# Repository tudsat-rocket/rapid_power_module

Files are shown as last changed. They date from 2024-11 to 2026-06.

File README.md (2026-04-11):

# Frodo Power Module

The battery boards for the FRoDO-rockets

## Version 1

@todo

## Version 2

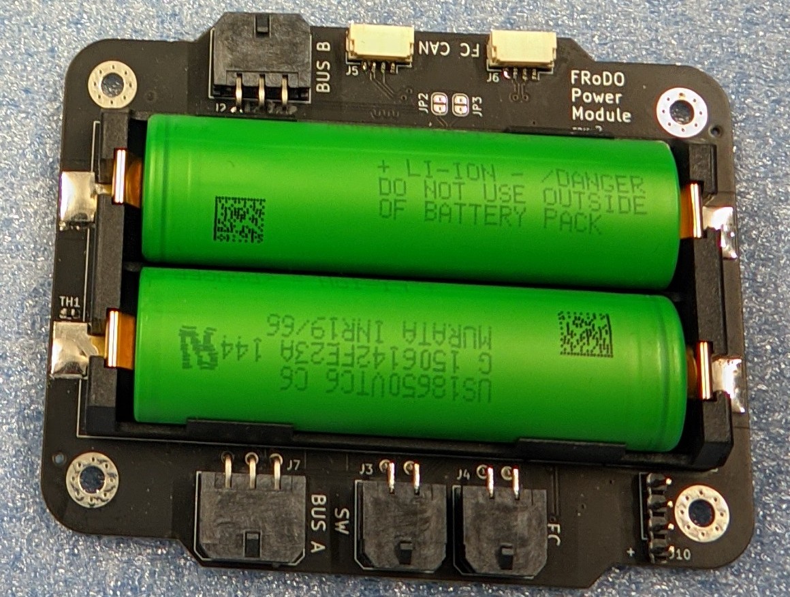
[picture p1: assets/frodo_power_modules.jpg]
battery-board


The newest version of the battery developed for the FRoDO-M-rocket 

The battery module contains two lithium-ion cells in series, mounted on an *SRAD* *PCB* using a Keystone connector, allowing the replacement of battery cells. 

The battery features a linear charging IC supporting up to 700 mA of charge current and performs balancing of the cells, powered by the charge bus through a reverse current protection diode and a PTC fuse.

### Components

- 2x 3000 mA h Sony VTC6 18650 lithium-ion cells in series
- for other components see https://github.com/tudsat-rocket/frodo_power_module/blob/main/frodo_power_module.csv

### Usage

| Connector | Purpose |
| --- | --- |
| FC | connect the flight computer. Outputs 8v with max ?a |
| SW | Switch to turn the battery board on and off |
| FC-CAN (2x) | CAN-bus for communication |
| BUS-A | |
| BUS-B | |

Spanning liegt von außen an, geht durch Arming Circuit,

## Version 3

tdb...

### ToDos for Hyacinth

- 3x 18650 lithium-ion cells in series

- New Charging IC due to more Cells

- Larger Board due to more Cells.

- Are 18650 a requirement or might they be exchanged against softbody batteries known from drones? (smaller PCB possible)

- Arming Schalter schaltet alles an.

- 

- 6 Pin durch 8 Pin ersetzen
  
  #### Possible new ICs

- https://www.ti.com/lit/ds/symlink/bq25820.pdf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

#### Ideas for Cell Voltage balancing

Good:
bq76PL536A: https://www.ti.com/lit/ds/symlink/bq76pl536a.pdf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 - Does not require host, is availabel on lcsc: https://www.lcsc.com/search?q=BQ76PL536A&s_z=n_BQ76PL536A
BQ76922: https://www.ti.com/lit/ds/symlink/bq76922.pdf?ts=1740361016781

Okay:
BQ79606A-Q1: https://www.ti.com/lit/ds/symlink/bq79606a-q1.pdf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 - Availability is bad

Meh:
BQ76925: https://www.ti.com/lit/ds/symlink/bq76925.pdf?ts=1740385881236 - due to required host. This is just an analogue expander.

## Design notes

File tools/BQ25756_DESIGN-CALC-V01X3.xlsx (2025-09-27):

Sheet: BQ2575X Design Calculator
 |  |  |  | BQ25756 Buck-Boost Battery Charger Design Calculator
 |  |  |  |  | View Password
 |  |  | = Input Box |  | BQ2575X
Step 1: Operating Specifications |  |  |  |  | Red Text = Conditional Formatting Conditions
 | Input Voltage - Min, VAC(min) | 4.2 | V | 4,2 V | 4.2 | 70
 | Input Voltage - Nom, VAC(nom) | 12 | V | 12 V | 4.2 | 70 | 4.2 | 24
 | Input Voltage - Max, VAC(max) | 24 | V | 24 V | 4.2 | 70
 | Battery Voltage, VBAT | 12.6 | V | 12,6 V | 3.3 | 70
 | Full Load Output Current, IOUT(max) | 6 | A | 6 A
 |  |  |  |  | Black Text = Lists or Formulas
Step 2: Switching Frequency
 | Desired Switching Frequency, FDFW | 500 | kHz | 500 kHz | 200 | 600
 | Recommended Switching Frequency Resistor, RFSW | 50.00 | kΩ | 50 kΩ
 | Selected Switching Frequency Resistor, RFSW | 50 | kΩ | 50 kΩ | 40 | 200
 | Recognized Switching Frequency, FSW | 500.00 | kHz |  | 475 | 525
 | Boost Duty Cycle Limitation | 88.75 | %
 | Boost Output Voltage Limitation at VAC(min) | 37.33333333 | V |  | 70 | 12.6
 | Boost Output Voltage Limitation at VAC(nom) | 70 | V |  | 70 | 12.6
 | Boost Output Voltage Limitation at VAC(max) | N/A | V |  | 70 | 12.6
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

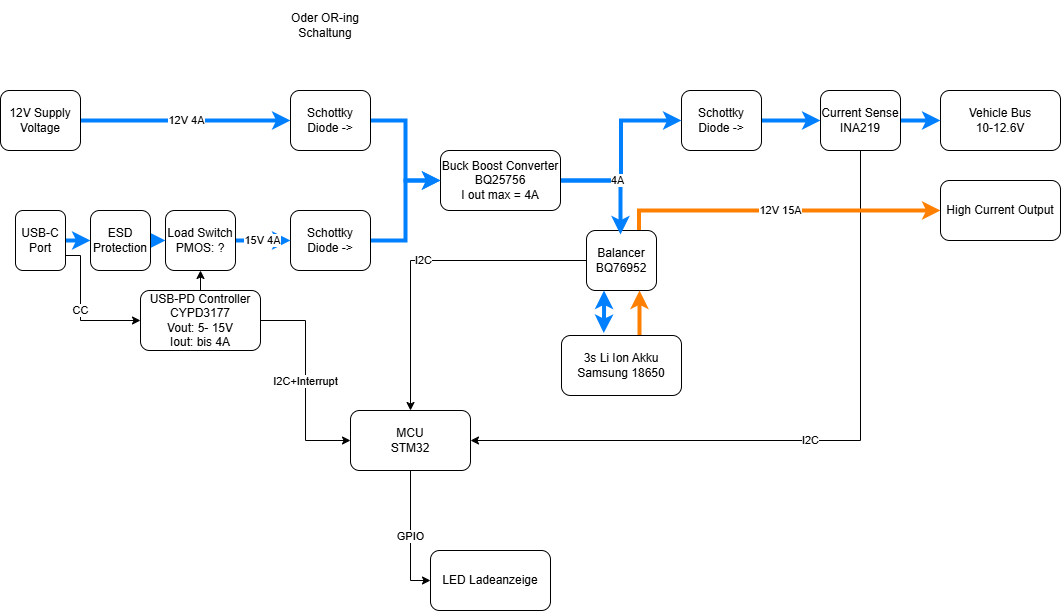
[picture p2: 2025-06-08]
docs/Power Board Overview.drawio.png

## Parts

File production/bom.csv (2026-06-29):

Designator | Footprint | Quantity | Value | LCSC Part #
C1, C2, C29, C31, C32, C33, C35, C42, C43, C44, C45, C46, C47, C48, C6, C8 | 0603 | 16 | 10u | C96446
C10, C14, C15, C16, C18, C19, C20, C21, C22, C34, C36, C41, C49, C5, C50, C51, C52 | 0402 | 17 | 100n | C307331
C11 | 1206 | 1 | 10u | C13585
C12 | 1206 | 1 | 22u | C12891
C13 | 0603 | 1 | 330n | C1615
C17, C37 | 0402 | 2 | 4u7 | C23733
C23, C27, C3, C4, C7, C9 | 0402 | 6 | 10n | C15195
C24, C26, C53, C54 | 0402 | 4 | 1u | C52923
C25, C28 | 0402 | 2 | 10p | C32949
C30 | 0805 | 1 | 2.2u | C377773
C38, C39 | 0402 | 2 | 47n | C82219
C40 | 0402 | 1 | 1n | C1523
C55 | 0402 | 1 | 100n | C1525
D1, D2, D3, D4, D5 | D_SMA | 5 | ~ | C22452
D10, D11, D12, D8, D9 | 0805 | 5 | green | C2297
D13, D6 | 0603 | 2 | red | C2286
D7 | 0805 | 1 | yellow | C2296
F1 | 2010 | 1 | 20A | C2762483
F2, F3 | 1206 | 2 | 5A | C48332
FB1 | 0603 | 1 | 120R | C14709
L1 | L_Wurth_WE-LQSH-3012 | 1 | 1u | C7423316
R1, R2, R3, R6, R7, R9 | 0402 | 6 | 22R | C25092
R10 | 0603 | 1 | 68k | C23231
R11, R13, R32, R38, R4, R5, R_TS_PU1 | 0402 | 7 | 10k | C25744
R12 | 0603 | 1 | 30k | C22984
R14, R16, R17, R18, R19, R20, R21, R22, R23, R35, R36 | 0402 | 11 | 1k | C11702
R15 | 0402 | 1 | 100k | C25741
R24 | 0603 | 1 | 2 | C22977
R25, R28 | 0402 | 2 | 10k | C25744
R26 | 0402 | 1 | 500R | C25123
R27 | 0603 | 1 | 20k | C4184
R29 | 0402 | 1 | 2k2 | C25879
R30 | 0603 | 1 | 5k24 | C23068
R31 | 0805 | 1 | 30k31 | C21841
R33 | 0402 | 1 | 100 | C25076
R34 | 2512 | 1 | 5m | C41382686
R37 | 0402 | 1 | 20k | C25765
R_IN1, R_IN2, R_IN3, R_IN4 | 0603 | 4 | 75 | C4275
R_LD1 | 0402 | 1 | 453k | C27009
SW1, SW2 | SW_SPST_TS-1088-xR020 | 2 | ~ | C720477
TP1, TP10, TP11, TP12, TP13, TP2, TP3, TP4, TP5, TP6, TP7, TP8, TP9 | TestPoint_Pad_D2.0mm | 13 | TestPoint
U1 | SOT-223-3_TabPin2 | 1 | AZ1117I-3.3 | C92102
U2 | SOT-563 | 1 | TPD4E1U06 | C527516
U3 | SOIC-8_3.9x4.9mm_P1.27mm | 1 | MCP2562-E-SN | C191417
U4 | TO-252-2 | 1 | L7805 | C58069
U5 | LQFP-64_10x10mm_P0.5mm | 1 | STM32F105RCTx | C8345
U6 | IC_BQ25798RQMR | 1 | BQ25798RQMR | C2876593
U7 | TSSOP-24_4.4x7.8mm_P0.65mm | 1 | BQ7791500PWR | C2876946
U8 | SOT-23-6 | 1 | INA181A1 | C2058943
U9 | SOT-23-5 | 1 | MCP6001-OT | C116490
Y1 | Crystal_SMD_5032-4Pin_5.0x3.2mm | 1 | 8MHz 12pF | C2149245

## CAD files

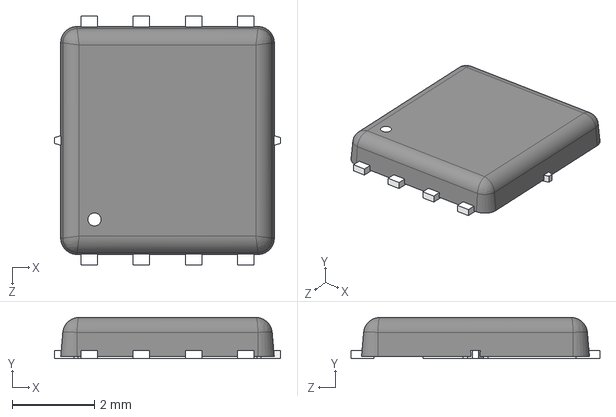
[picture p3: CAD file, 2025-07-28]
AONS66614.STEP
5.50 x 1.00 x 6.05 mm

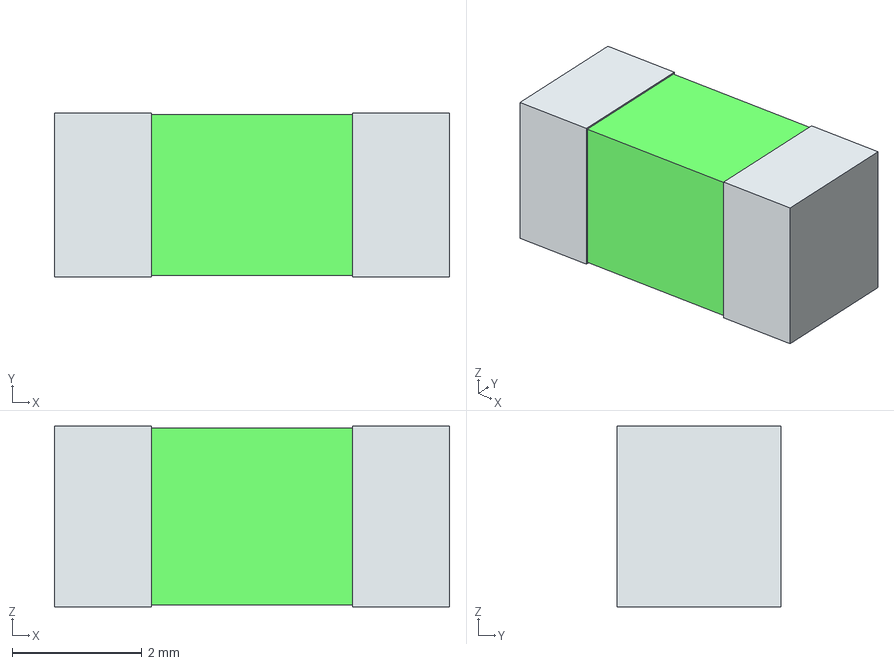
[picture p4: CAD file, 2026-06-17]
common/3dModels/Fuse_2410_0679L9200-05.stp
6.10 x 2.54 x 2.79 mm
term1
term2

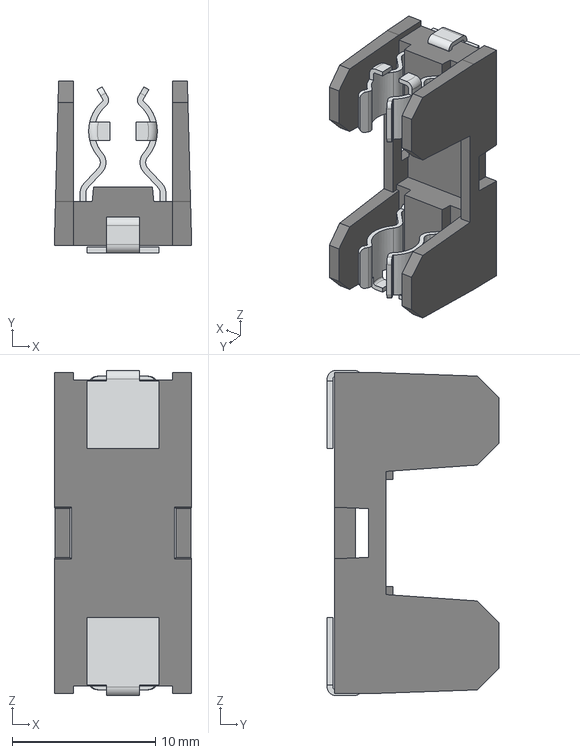
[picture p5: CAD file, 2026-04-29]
common/3dModels/Würth_fuse_holder_696103101002 (rev1).step
9.60 x 12.0 x 22.7 mm

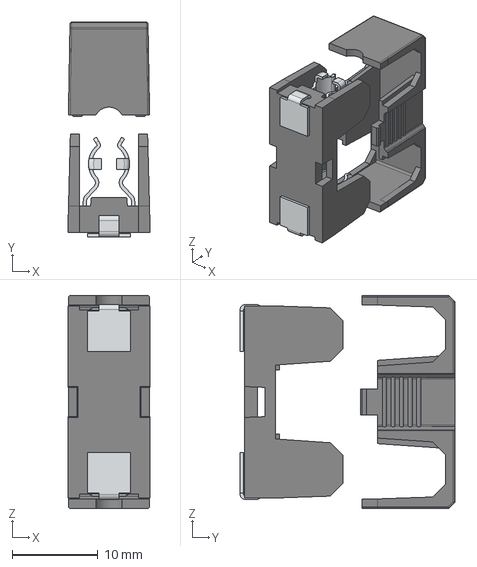
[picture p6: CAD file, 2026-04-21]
common/3dModels/20A_fuse.stp
9.60 x 25.0 x 24.8 mm
PTF18SMD
BS613

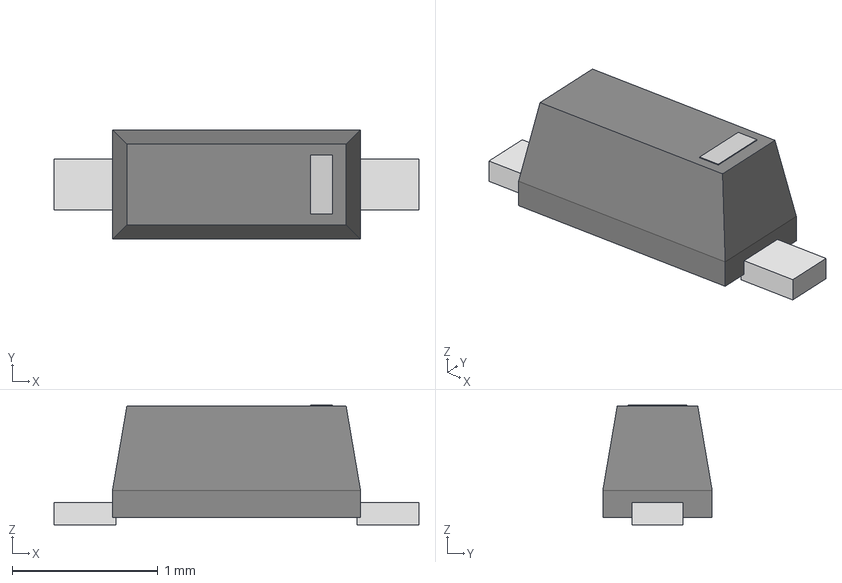
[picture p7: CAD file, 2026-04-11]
common/3dModels/SOD323F_DIO.step
2.50 x 0.75 x 0.819 mm

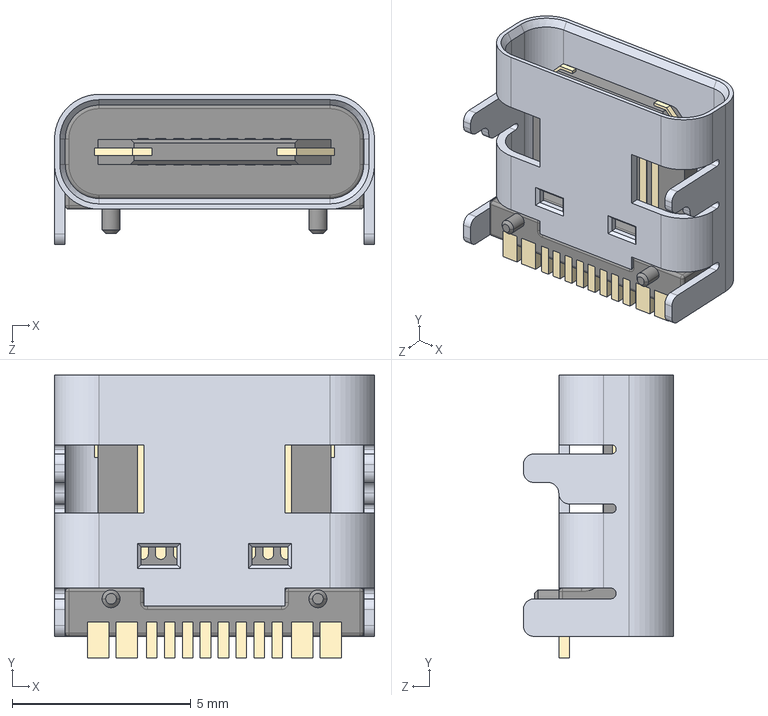
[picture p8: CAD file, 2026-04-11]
common/3dModels/usb_c.step
8.94 x 7.90 x 4.20 mm

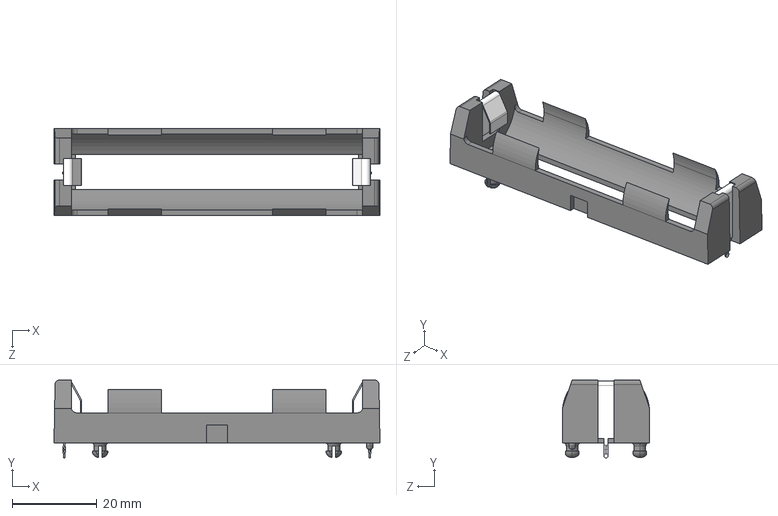
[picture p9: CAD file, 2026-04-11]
common/3dModels/Battery Holder 18650 1043.step
77.1 x 18.4 x 20.7 mm

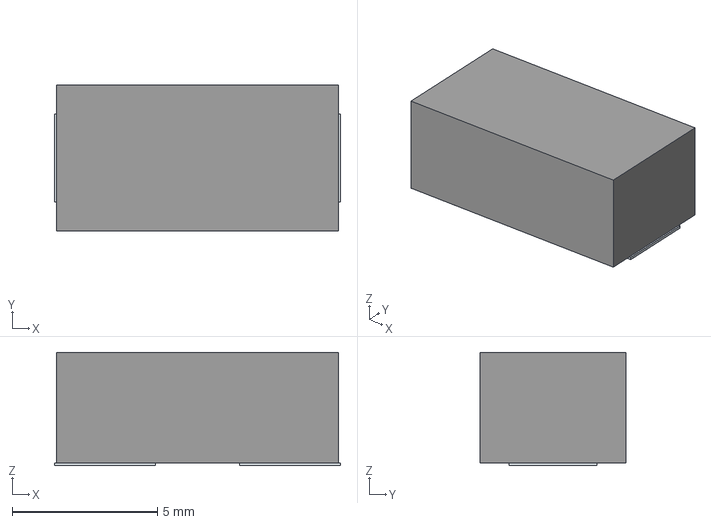
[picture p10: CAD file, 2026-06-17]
common/3dModels/0154005.stp
9.86 x 5.03 x 3.91 mm
Pins

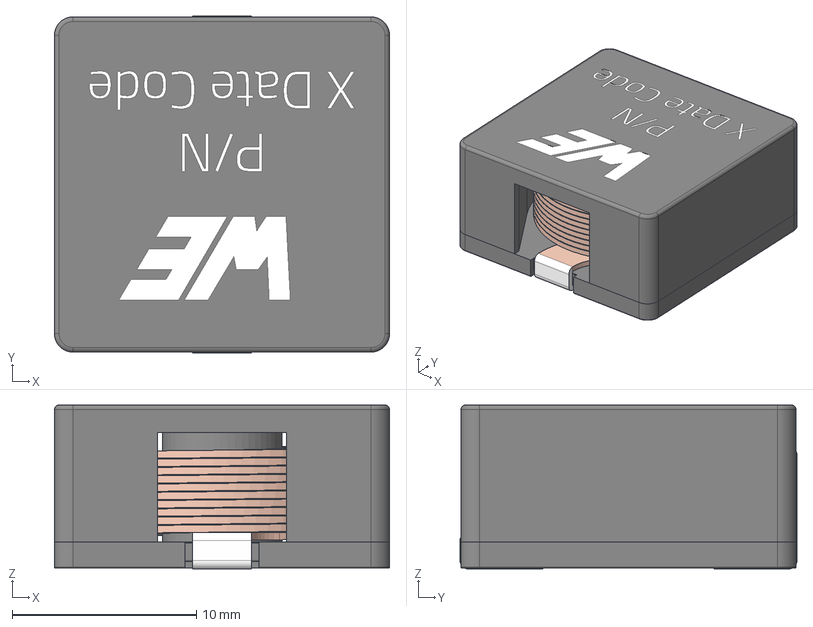
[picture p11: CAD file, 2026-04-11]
common/3dModels/o54893v246 WE-HCI_1890_7443557 (rev1).stp
18.2 x 18.3 x 8.90 mm
Gehäuse
Boden
Spule

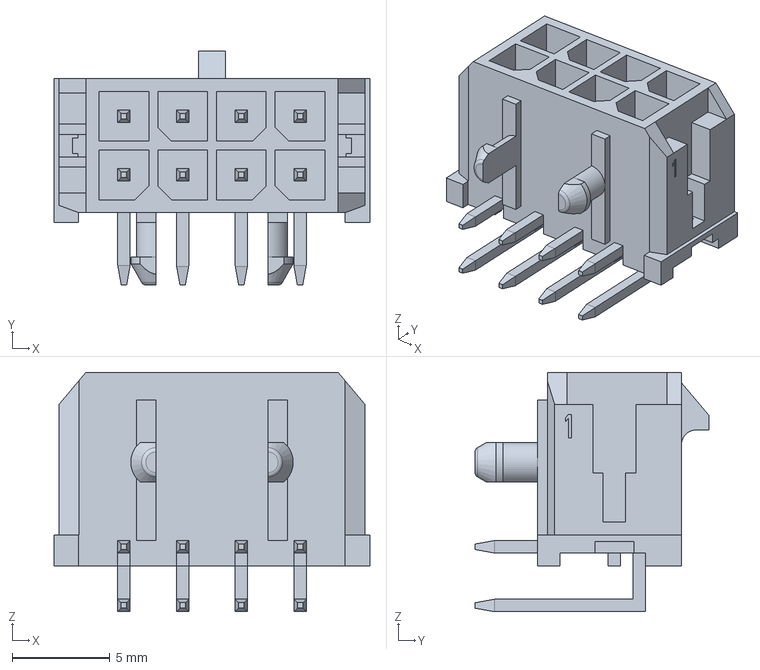
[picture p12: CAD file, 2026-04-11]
common/3dModels/430450800.stp
16.1 x 11.9 x 12.2 mm

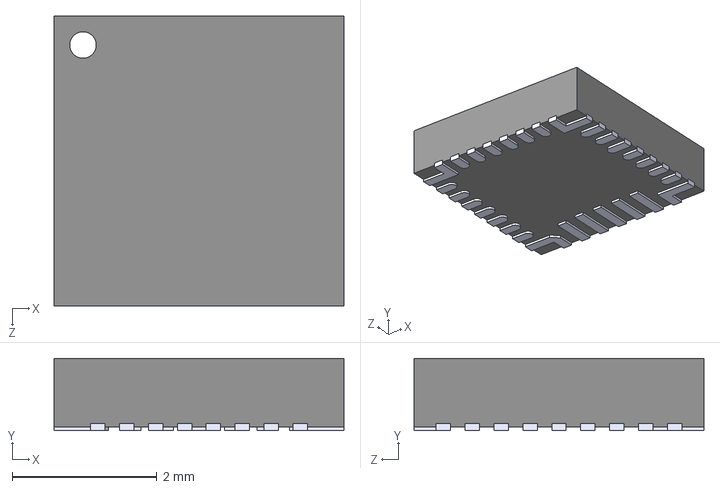
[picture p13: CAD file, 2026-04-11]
common/3dModels/BQ25798RQMR.step
4.00 x 1.00 x 4.00 mm

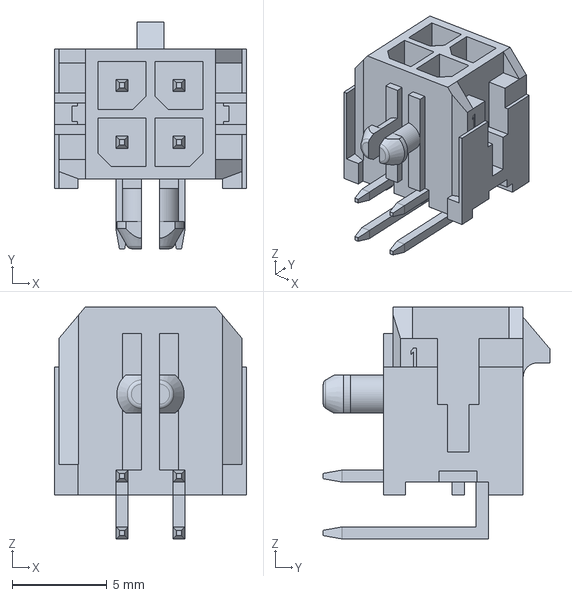
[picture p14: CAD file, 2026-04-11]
common/3dModels/430450400.step
10.2 x 11.9 x 12.2 mm

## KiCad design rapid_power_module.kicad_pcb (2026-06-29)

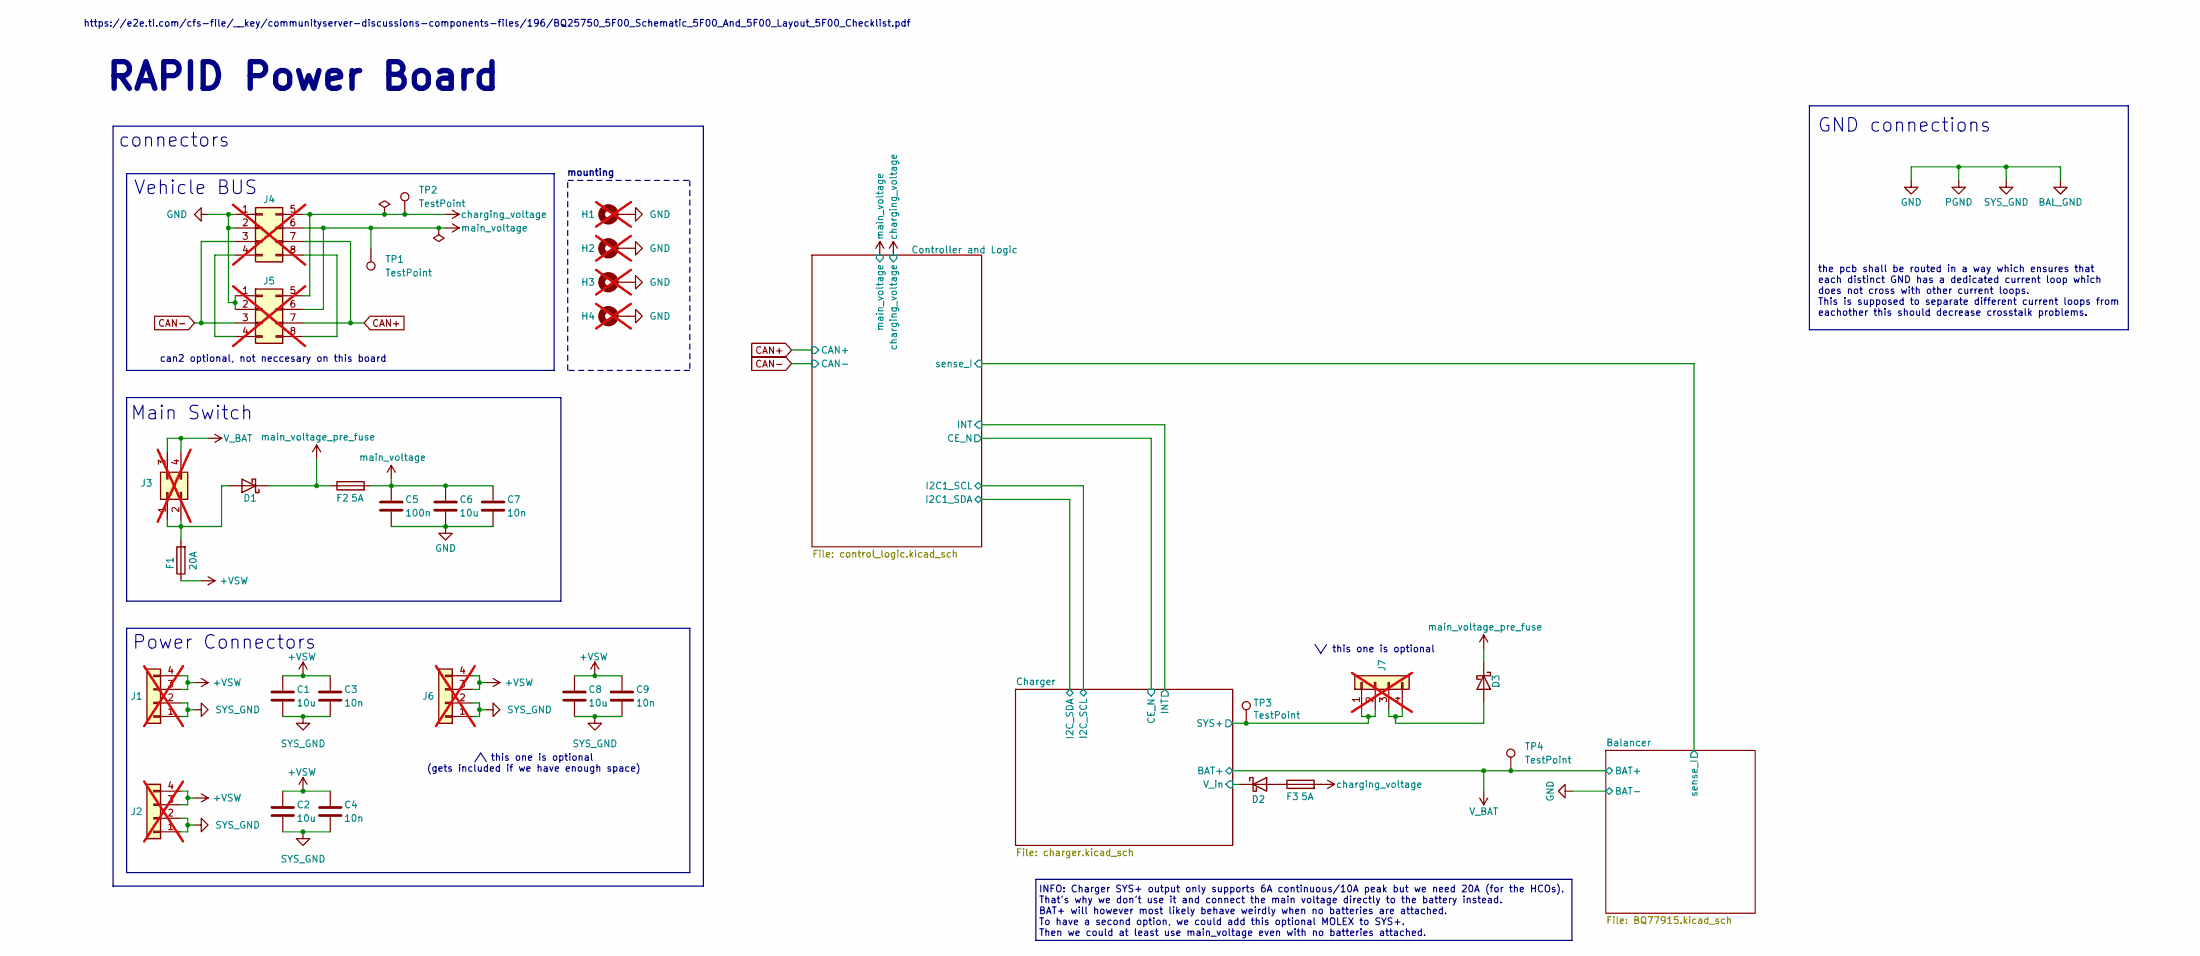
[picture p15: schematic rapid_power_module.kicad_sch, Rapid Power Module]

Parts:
C1, C2, C6, C8: 10u; C_0603_1608Metric; LCSC C96446
C3, C4, C7, C9: 10n; C_0402_1005Metric; LCSC C15195
C5: 100n; C_0402_1005Metric; LCSC C307331
D1, D2, D3: D_SMA; LCSC C22452
F1: 20A; Fuse_2010_5025Metric_Pad1.52x2.65mm_HandSolder; LCSC C2762483
F2, F3: 5A; Fuse_1206_3216Metric_Pad1.42x1.75mm_HandSolder; LCSC C48332
H1, H2, H3, H4: MountingHole_Pad; MountingHole_3.2mm_M3_Pad_Via; LCSC x; not fitted
J1, J2: Molex MicroFit 2x2; Molex_Micro-Fit_3.0_43045-0400_2x02_P3.00mm_Horizontal; Part# 0430450400; LCSC C122413; not fitted
J3: Molex MicroFit 2x2; Molex_Micro-Fit_3.0_43045-0400_2x02_P3.00mm_Horizontal; LCSC C122413; not fitted
J4, J5: Conn_02x04_Top_Bottom; Molex_Micro-Fit_3.0_43045-0800_2x04_P3.00mm_Horizontal; LCSC x; not fitted
J6, J7: Molex MicroFit 2x2; Molex_Micro-Fit_3.0_43045-0400_2x02_P3.00mm_Horizontal; Part# 0430450400; LCSC# C122413; not fitted
TP1, TP2, TP3, TP4: TestPoint; TestPoint_Pad_D2.0mm

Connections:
+VSW: C1.1, C2.1, C3.1, C4.1, C8.1, C9.1, F1.1, J1.3, J1.4, J2.3, J2.4, J6.3, J6.4
/Charger/SYS+: J7.1, J7.2, TP3.1 (1_1); also elsewhere on the board
/Charger/V_in: D2.1 (K); also elsewhere on the board
BAL_GND: C1.2, C2.2, C3.2, C4.2, C5.2, C6.2, C7.2, C8.2, C9.2, H1.1 (1_1), H2.1 (1_1), H3.1 (1_1), H4.1 (1_1), J1.1, J1.2, J2.1, J2.2, J4.1, J4.2, J5.1, J5.2, J6.1, J6.2; also elsewhere on the board
CAN+: J4.7, J5.7; also elsewhere on the board
CAN-: J4.3, J5.3; also elsewhere on the board
unnamed: D1.2 (A), F1.2, J3.1, J3.2
unnamed: D2.2 (A), F3.1
unnamed: D3.2 (A), J7.3, J7.4
unnamed: J4.4, J5.4
unnamed: J4.8, J5.8
V_BAT: J3.3, J3.4, TP4.1 (1_1); also elsewhere on the board
charging_voltage: F3.2, J4.5, J5.5, TP2.1 (1_1); also elsewhere on the board
main_voltage: C5.1, C6.1, C7.1, F2.2, J4.6, J5.6, TP1.1 (1_1); also elsewhere on the board
main_voltage_pre_fuse: D1.1 (K), D3.1 (K), F2.1

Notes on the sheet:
the pcb shall be routed in a way which ensures that each distinct GND has a dedicated current loop which does not cross with other current loops. This is supposed to separate different current loops from eachother this should decrease crosstalk problems.
connectors
can2 optional, not neccesary on this board
Vehicle BUS
Main Switch
RAPID Power Board
https://e2e.ti.com/cfs-file/__key/communityserver-discussions-components-files/196/BQ25750_5F00_Schematic_5F00_And_5F00_Layout_5F00_Checklist.pdf
\/ this one is optional
INFO: Charger SYS+ output only supports 6A continuous/10A peak but we need 20A (for the HCOs). That's why we don't use it and connect the main voltage directly to the battery instead. BAT+ will however most likely behave weirdly when no batteries are attached. To have a second option, we could add 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
mounting
/\ this one is optional (gets included if we have enough space)
Power Connectors
GND connections

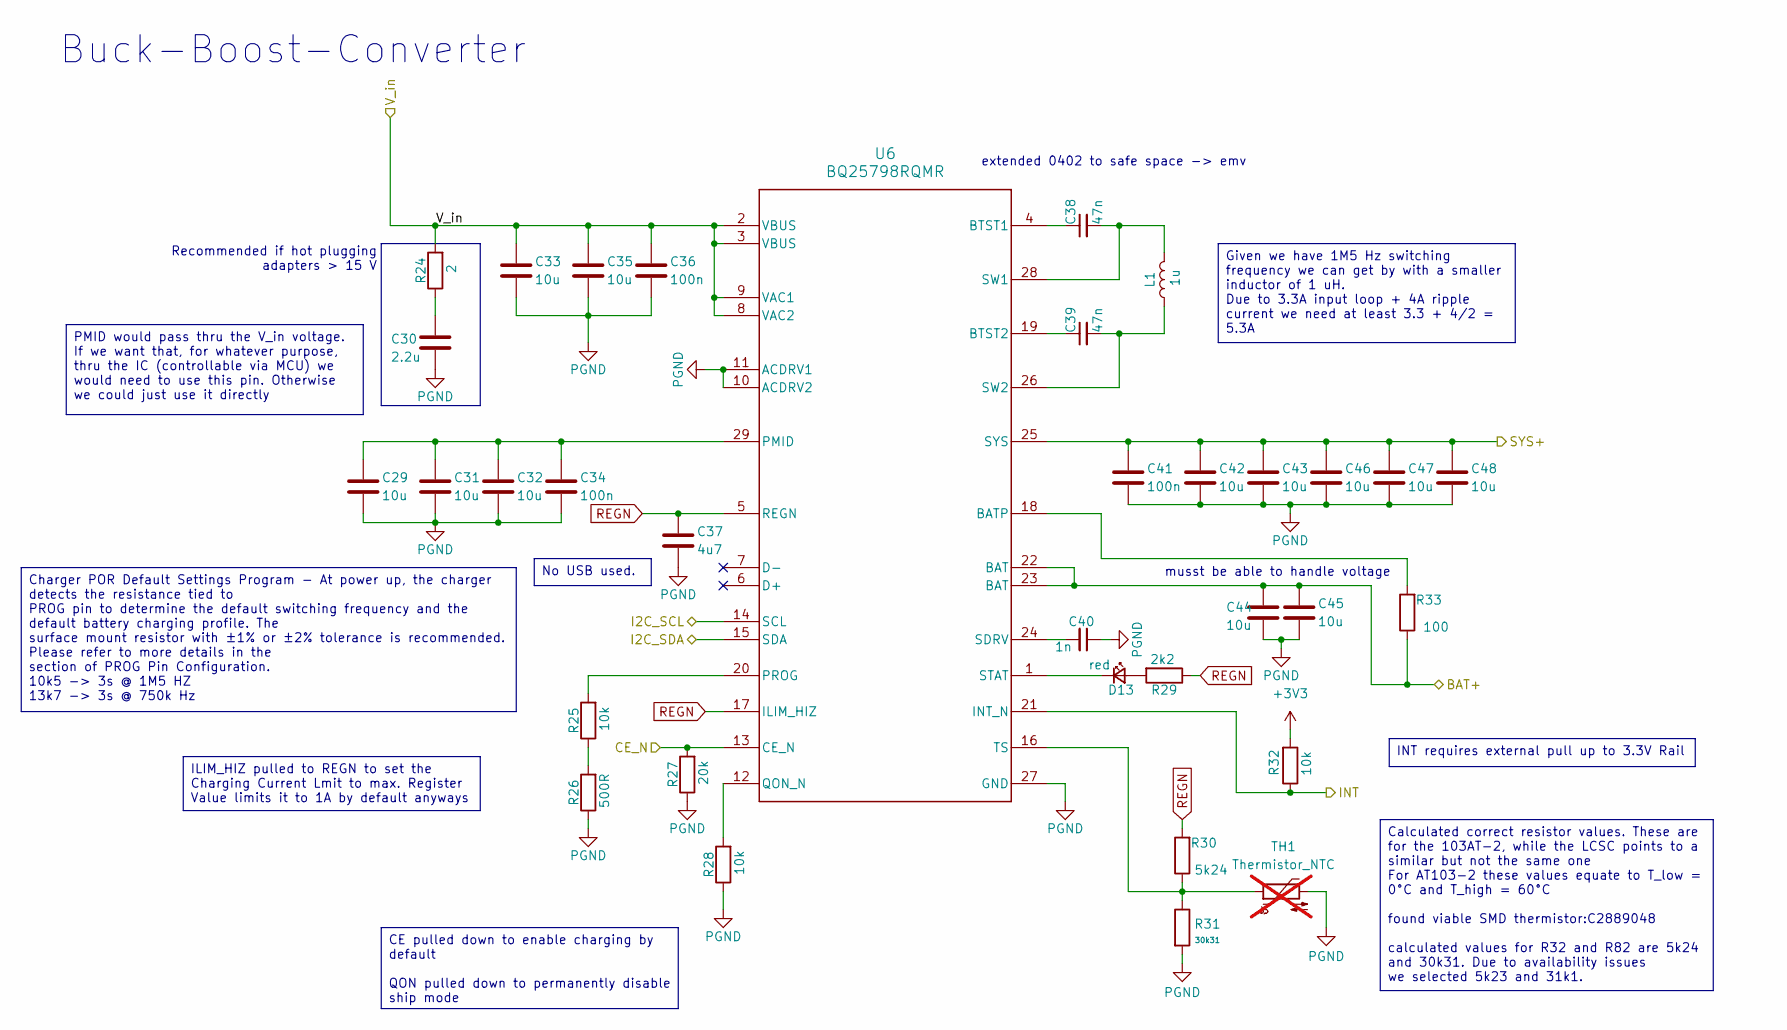
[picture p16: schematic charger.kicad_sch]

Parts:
C29, C31, C32, C33, C35, C42, C43, C44, C45, C46, C47, C48: 10u; C_0603_1608Metric; LCSC C96446
C30: 2.2u; C_0805_2012Metric; LCSC C377773
C34, C36, C41: 100n; C_0402_1005Metric; LCSC C307331
C37: 4u7; C_0402_1005Metric; LCSC C23733
C38, C39: 47n; C_0402_1005Metric; LCSC C82219
C40: 1n; C_0402_1005Metric; LCSC C1523
D13: red; LED_0603_1608Metric; LCSC C2286
L1: 1u; L_Wurth_WE-LQSH-3012; LCSC C7423316
R24: 2; R_0603_1608Metric; LCSC C22977
R25, R28, R32: 10k; R_0402_1005Metric; LCSC C25744
R26: 500R; R_0402_1005Metric; LCSC C25123
R27: 20k; R_0603_1608Metric; LCSC C4184
R29: 2k2; R_0402_1005Metric; LCSC C25879
R30: 5k24; R_0603_1608Metric; LCSC C23068
R31: 30k31; R_0805_2012Metric; LCSC C21841
R33: 100; R_0402_1005Metric; LCSC C25076
TH1: Thermistor_NTC; R_0603_1608Metric_Pad0.98x0.95mm_HandSolder; LCSC C2889048; not fitted
U6: BQ25798RQMR; IC_BQ25798RQMR; LCSC C2876593

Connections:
+3V3: R32.2; also elsewhere on the board
/Charger/CE_N: R27.2, U6.13 (CE_N); also elsewhere on the board
/Charger/INT: R32.1, U6.21 (INT_N); also elsewhere on the board
/Charger/SYS+: C41.1, C42.1, C43.1, C46.1, C47.1, C48.1, U6.25 (SYS); also elsewhere on the board
/Charger/V_in: C33.1, C35.1, C36.1, R24.2, U6.2 (VBUS), U6.3 (VBUS), U6.8 (VAC2), U6.9 (VAC1); also elsewhere on the board
BAL_GND: C29.2, C30.2, C31.2, C32.2, C33.2, C34.2, C35.2, C36.2, C37.2, C40.1, C41.2, C42.2, C43.2, C44.2, C45.2, C46.2, C47.2, C48.2, R26.1, R27.1, R28.1, R31.2, TH1.2, U6.10 (ACDRV2), U6.11 (ACDRV1), U6.27 (GND); also elsewhere on the board
I2C1_SCL: U6.14 (SCL); also elsewhere on the board
I2C1_SDA: U6.15 (SDA); also elsewhere on the board
unnamed: C30.1, R24.1
unnamed: D13.2 (A), R29.2
unnamed: D13.1 (K), U6.1 (STAT)
unnamed: R25.1, R26.2
unnamed: R33.2, U6.18 (BATP)
unnamed: C38.1, U6.4 (BTST1)
unnamed: C39.1, U6.19 (BTST2)
unnamed: C29.1, C31.1, C32.1, C34.1, U6.29 (PMID)
unnamed: R25.2, U6.20 (PROG)
unnamed: R28.2, U6.12 (QON_N)
unnamed: C40.2, U6.24 (SDRV)
unnamed: C38.2, L1.2, U6.28 (SW1)
unnamed: C39.2, L1.1, U6.26 (SW2)
unnamed: R30.1, R31.1, TH1.1, U6.16 (TS)
REGN: C37.1, R29.1, R30.2, U6.5 (REGN), U6.17 (ILIM_HIZ)
V_BAT: C44.1, C45.1, R33.1, U6.22 (BAT), U6.23 (BAT); also elsewhere on the board

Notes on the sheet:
extended 0402 to safe space -> emv
Buck-Boost-Converter
Recommended if hot plugging adapters > 15 V
musst be able to handle voltage
ILIM_HIZ pulled to REGN to set the Charging Current Lmit to max. Register Value limits it to 1A by default anyways
Given we have 1M5 Hz switching frequency we can get by with a smaller inductor of 1 uH. Due to 3.3A input loop + 4A ripple current we need at least 3.3 + 4/2 = 5.3A
INT requires external pull up to 3.3V Rail
Calculated correct resistor values. These are for the 103AT-2, while the LCSC points to a similar but not the same one For AT103-2 these values equate to T_low = 0°C and T_high = 60°C found viable SMD thermistor:C2889048 calculated values for R32 and R82 are 5k24 and 30k31. Due to availability issu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
PMID would pass thru the V_in voltage. If we want that, for whatever purpose, thru the IC (controllable via MCU) we would need to use this pin. Otherwise we could just use it directly
CE pulled down to enable charging by default QON pulled down to permanently disable ship mode
No USB used.
Charger POR Default Settings Program - At power up, the charger detects the resistance tied to PROG pin to determine the default switching frequency and the default battery charging profile. The surface mount resistor with ±1% or ±2% tolerance is recommended. Please refer to more details in the sec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

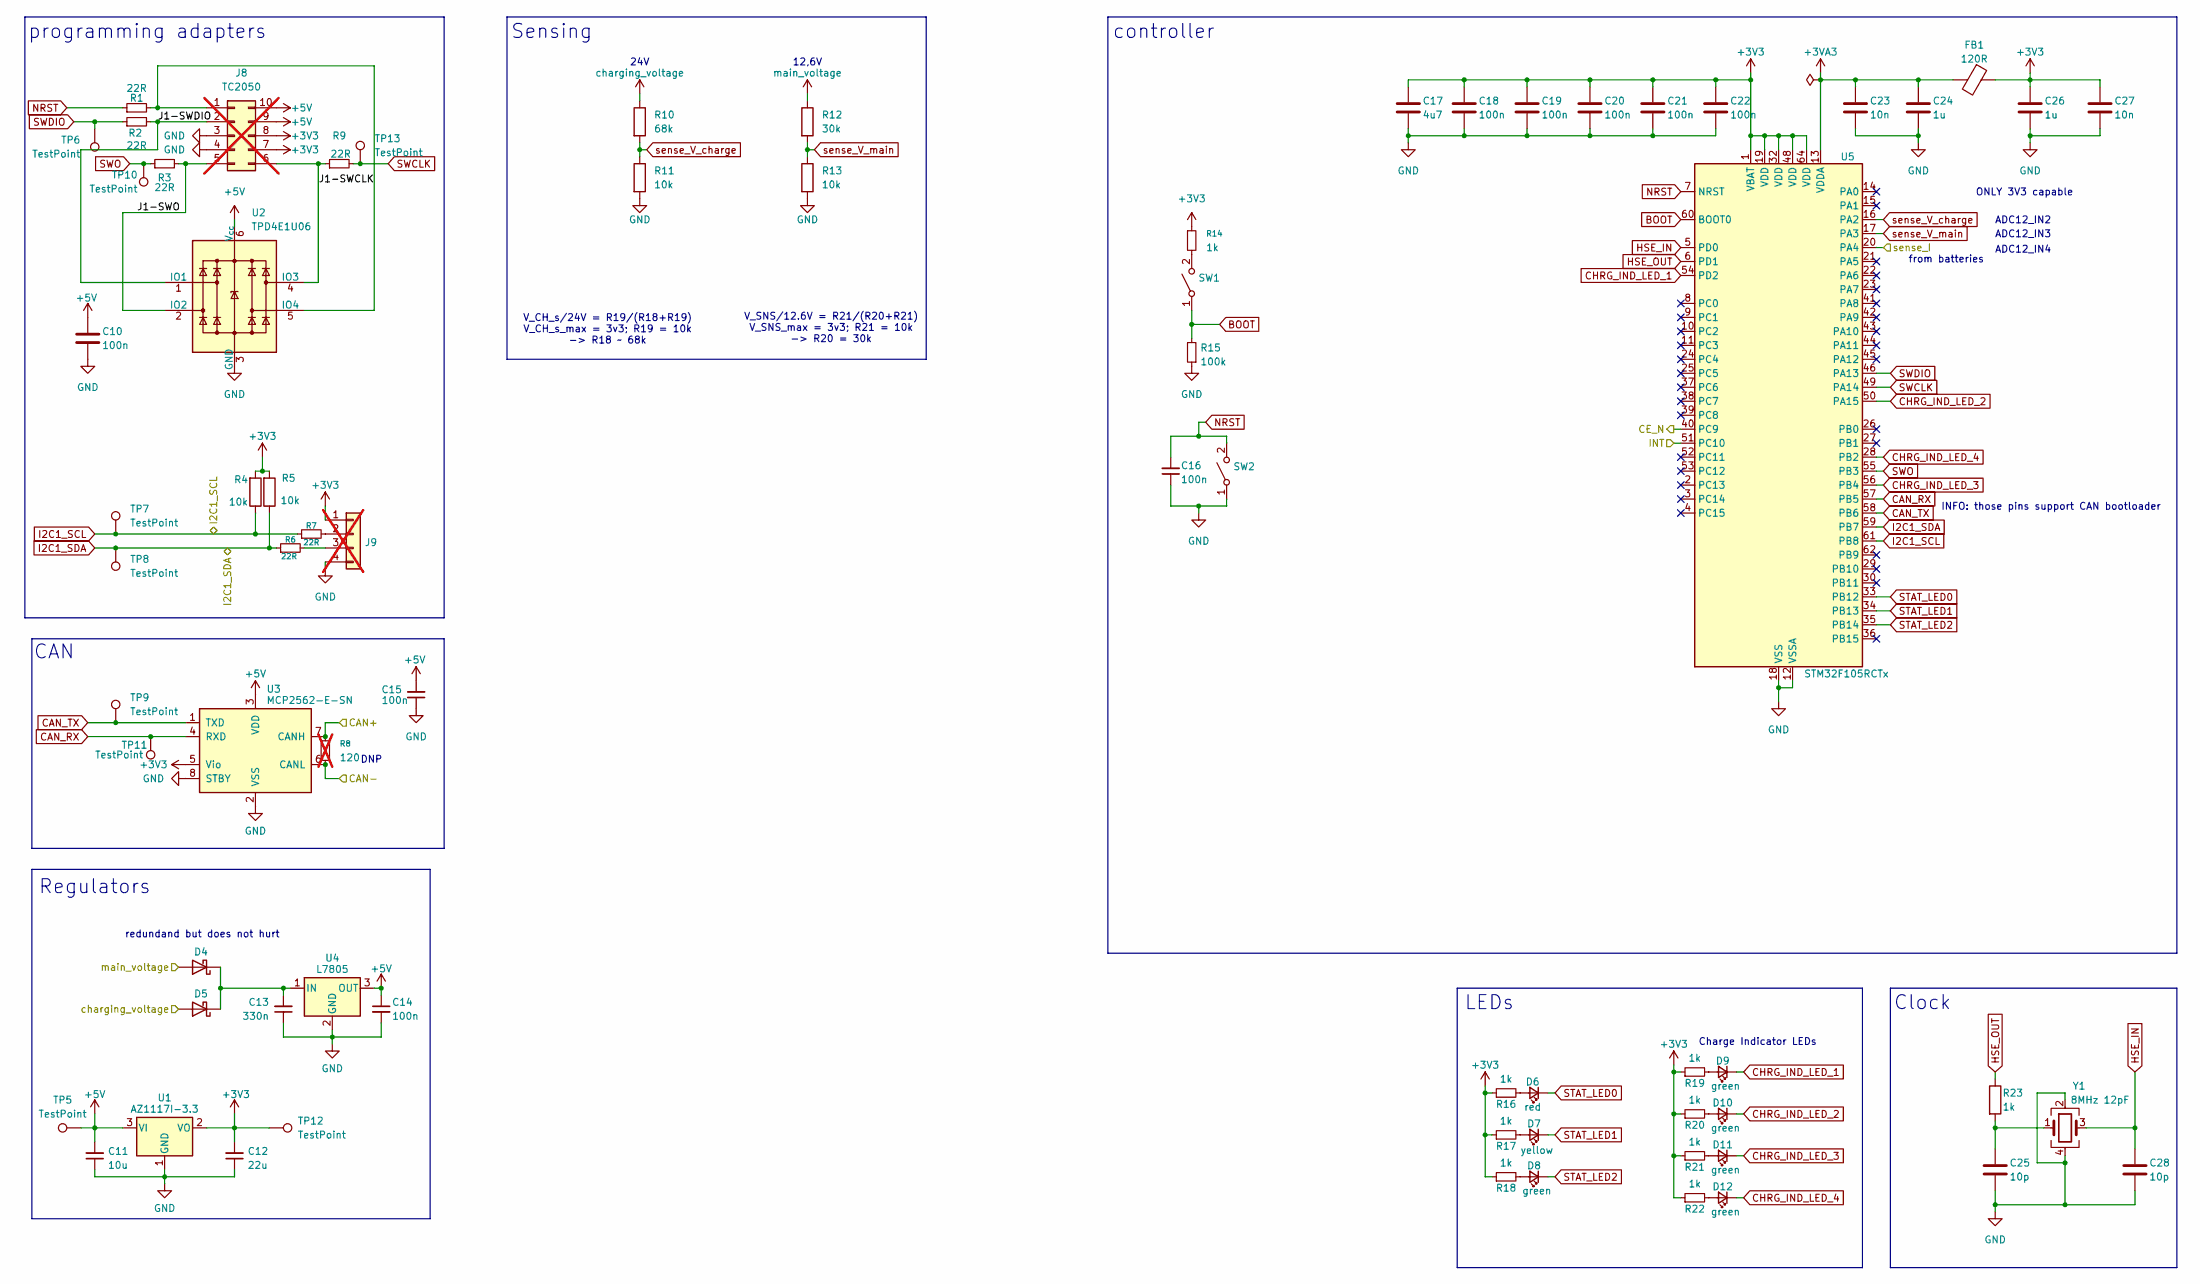
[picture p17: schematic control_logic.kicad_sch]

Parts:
C10, C15, C18, C19, C20, C21, C22: 100n; C_0402_1005Metric; LCSC C307331
C11: 10u; C_1206_3216Metric; Part# CL31A106KBHNNNE; LCSC C13585
C12: 22u; C_1206_3216Metric; Part# CL31A226KAHNNNE; LCSC C12891
C13: 330n; C_0603_1608Metric; Part# CL10B474KA8NNNC; LCSC C1615
C14: 100n; C_0402_1005Metric; Part# CC0603KRX7R9BB104; LCSC C307331
C16: 100n; C_0402_1005Metric; Part# CL10B104KB8NNNC; LCSC C307331
C17: 4u7; C_0402_1005Metric; LCSC C23733
C23, C27: 10n; C_0402_1005Metric; LCSC C15195
C24, C26: 1u; C_0402_1005Metric; LCSC C52923
C25, C28: 10p; C_0402_1005Metric; LCSC C32949
D4, D5: D_SMA; LCSC C22452
D6: red; LED_0603_1608Metric; LCSC C2286
D7: yellow; LED_0805_2012Metric; LCSC C2296
D8, D9, D10, D11, D12: green; LED_0805_2012Metric; LCSC C2297
FB1: 120R; L_0603_1608Metric; Part# BLM18PG121SN1D; LCSC C14709
J8: TC2050; Tag-Connect_TC2050-IDC-FP_2x05_P1.27mm_Vertical; LCSC x; not fitted
J9: SWD Header; PinHeader_1x04_P2.54mm_Vertical_SMD_Pin1Left; LCSC x; not fitted
R1, R2, R3, R9: 22R; R_0402_1005Metric; Part# RC0603FR-0710KL; LCSC C25092
R4, R5, R11, R13: 10k; R_0402_1005Metric; LCSC C25744
R6, R7: 22R; R_0402_1005Metric; Part# RC0603FR-0722RL; LCSC C25092
R8: 120; C_0402_1005Metric; LCSC C25079; not fitted
R10: 68k; R_0603_1608Metric; LCSC C23231
R12: 30k; R_0603_1608Metric; LCSC C22984
R14, R16, R17, R18, R19, R20, R21, R22, R23: 1k; R_0402_1005Metric; LCSC C11702
R15: 100k; R_0402_1005Metric; Part# RC0603FR-0710KL; LCSC C25741
SW1, SW2: SW_SPST_TS-1088-xR020; LCSC C720477
TP5, TP6, TP7, TP8, TP9, TP10, TP11, TP12, TP13: TestPoint; TestPoint_Pad_D2.0mm
U1: AZ1117I-3.3; SOT-223-3_TabPin2; Part# AZ1117CH-3.3TRG1; LCSC C92102
U2: TPD4E1U06; SOT-563; LCSC C527516
U3: MCP2562-E-SN; SOIC-8_3.9x4.9mm_P1.27mm; Part# MCP2562-H/SN; DigiKey# MCP2562-H/SN
U4: L7805; TO-252-2; Part# L78M05ABDT-TR; LCSC C58069
U5: STM32F105RCTx; LQFP-64_10x10mm_P0.5mm; LCSC C8345
Y1: 8MHz 12pF; Crystal_SMD_5032-4Pin_5.0x3.2mm; Part# 5TJ480000NYLBC; LCSC C2149245

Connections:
+3V3: C12.2, C17.1, C18.1, C19.1, C20.1, C21.1, C22.1, C26.1, C27.1, FB1.1, J8.7, J8.8, J9.1, R4.2, R5.2, R14.1, R16.1, R17.1, R18.1, R19.1, R20.1, R21.1, R22.1, TP12.1 (1_1), U1.2 (VO), U3.5 (Vio), U5.1 (VBAT), U5.19 (VDD), U5.32 (VDD), U5.48 (VDD), U5.64 (VDD); also elsewhere on the board
+3VA3: C23.1, C24.1, FB1.2, U5.13 (VDDA)
+5V: C10.1, C11.2, C14.1, C15.2, J8.9, J8.10, TP5.1 (1_1), U1.3 (VI), U2.6 (V_{cc}), U3.3 (VDD), U4.3 (OUT)
/Balancer/sense_I: U5.20 (PA4); also elsewhere on the board
/Charger/CE_N: U5.40 (PC9); also elsewhere on the board
/Charger/INT: U5.51 (PC10); also elsewhere on the board
/Controller and Logic/J1-SWCLK: J8.6, R9.1, U2.4 (IO3)
/Controller and Logic/J1-SWDIO: J8.2, R2.2, U2.1 (IO1)
/Controller and Logic/J1-SWO: J8.5, R3.2, U2.2 (IO2)
BAL_GND: C10.2, C11.1, C12.1, C13.1, C14.2, C15.1, C16.1, C17.2, C18.2, C19.2, C20.2, C21.2, C22.2, C23.2, C24.2, C25.2, C26.2, C27.2, C28.2, J8.3, J8.4, J9.4, R11.2, R13.2, R15.1, SW2.1 (A), U1.1 (GND), U2.3 (GND), U3.2 (VSS), U3.8 (STBY), U4.2 (GND), U5.12 (VSSA), U5.18 (VSS), U5.31 (VSS), U5.47 (VSS), U5.63 (VSS), Y1.2, Y1.4; also elsewhere on the board
BOOT: R15.2, SW1.1 (A), U5.60 (BOOT0)
CAN+: R8.1, U3.7 (CANH); also elsewhere on the board
CAN-: R8.2, U3.6 (CANL); also elsewhere on the board
CAN_RX: TP11.1 (1_1), U3.4 (RXD), U5.57 (PB5)
CAN_TX: TP9.1 (1_1), U3.1 (TXD), U5.58 (PB6)
CHRG_IND_LED_1: D9.1 (K), U5.54 (PD2)
CHRG_IND_LED_2: D10.1 (K), U5.50 (PA15)
CHRG_IND_LED_3: D11.1 (K), U5.56 (PB4)
CHRG_IND_LED_4: D12.1 (K), U5.28 (PB2)
HSE_IN: C28.1, U5.5 (PD0), Y1.3
HSE_OUT: R23.1, U5.6 (PD1)
I2C1_SCL: R4.1, R7.1, TP7.1 (1_1), U5.61 (PB8); also elsewhere on the board
I2C1_SDA: R5.1, R6.1, TP8.1 (1_1), U5.59 (PB7); also elsewhere on the board
NRST: C16.2, R1.1, SW2.2 (B), U5.7 (NRST)
unnamed: C25.1, R23.2, Y1.1
unnamed: C13.2, D4.1 (K), D5.1 (K), U4.1 (IN)
unnamed: D6.2 (A), R16.2
unnamed: D7.2 (A), R17.2
unnamed: D8.2 (A), R18.2
unnamed: D9.2 (A), R19.2
unnamed: D10.2 (A), R20.2
unnamed: D11.2 (A), R21.2
unnamed: D12.2 (A), R22.2
unnamed: J8.1, R1.2, U2.5 (IO4)
unnamed: J9.2, R7.2
unnamed: J9.3, R6.2
unnamed: R14.2, SW1.2 (B)
STAT_LED0: D6.1 (K), U5.33 (PB12)
STAT_LED1: D7.1 (K), U5.34 (PB13)
STAT_LED2: D8.1 (K), U5.35 (PB14)
SWCLK: R9.2, TP13.1 (1_1), U5.49 (PA14)
SWDIO: R2.1, TP6.1 (1_1), U5.46 (PA13)
SWO: R3.1, TP10.1 (1_1), U5.55 (PB3)
charging_voltage: D5.2 (A), R10.1; also elsewhere on the board
main_voltage: D4.2 (A), R12.1; also elsewhere on the board
sense_V_charge: R10.2, R11.1, U5.16 (PA2)
sense_V_main: R12.2, R13.1, U5.17 (PA3)

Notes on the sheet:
Clock
INFO: those pins support CAN bootloader
controller
from batteries
Sensing
Charge Indicator LEDs
Regulators
redundand but does not hurt
V_SNS/12.6V = R21/(R20+R21) V_SNS_max = 3v3; R21 = 10k -> R20 = 30k
LEDs
ADC12_IN3
ADC12_IN4
programming adapters
ONLY 3V3 capable
12,6V
ADC12_IN2
DNP
CAN
24V
V_CH_s/24V = R19/(R18+R19) V_CH_s_max = 3v3; R19 = 10k -> R18 ~ 68k

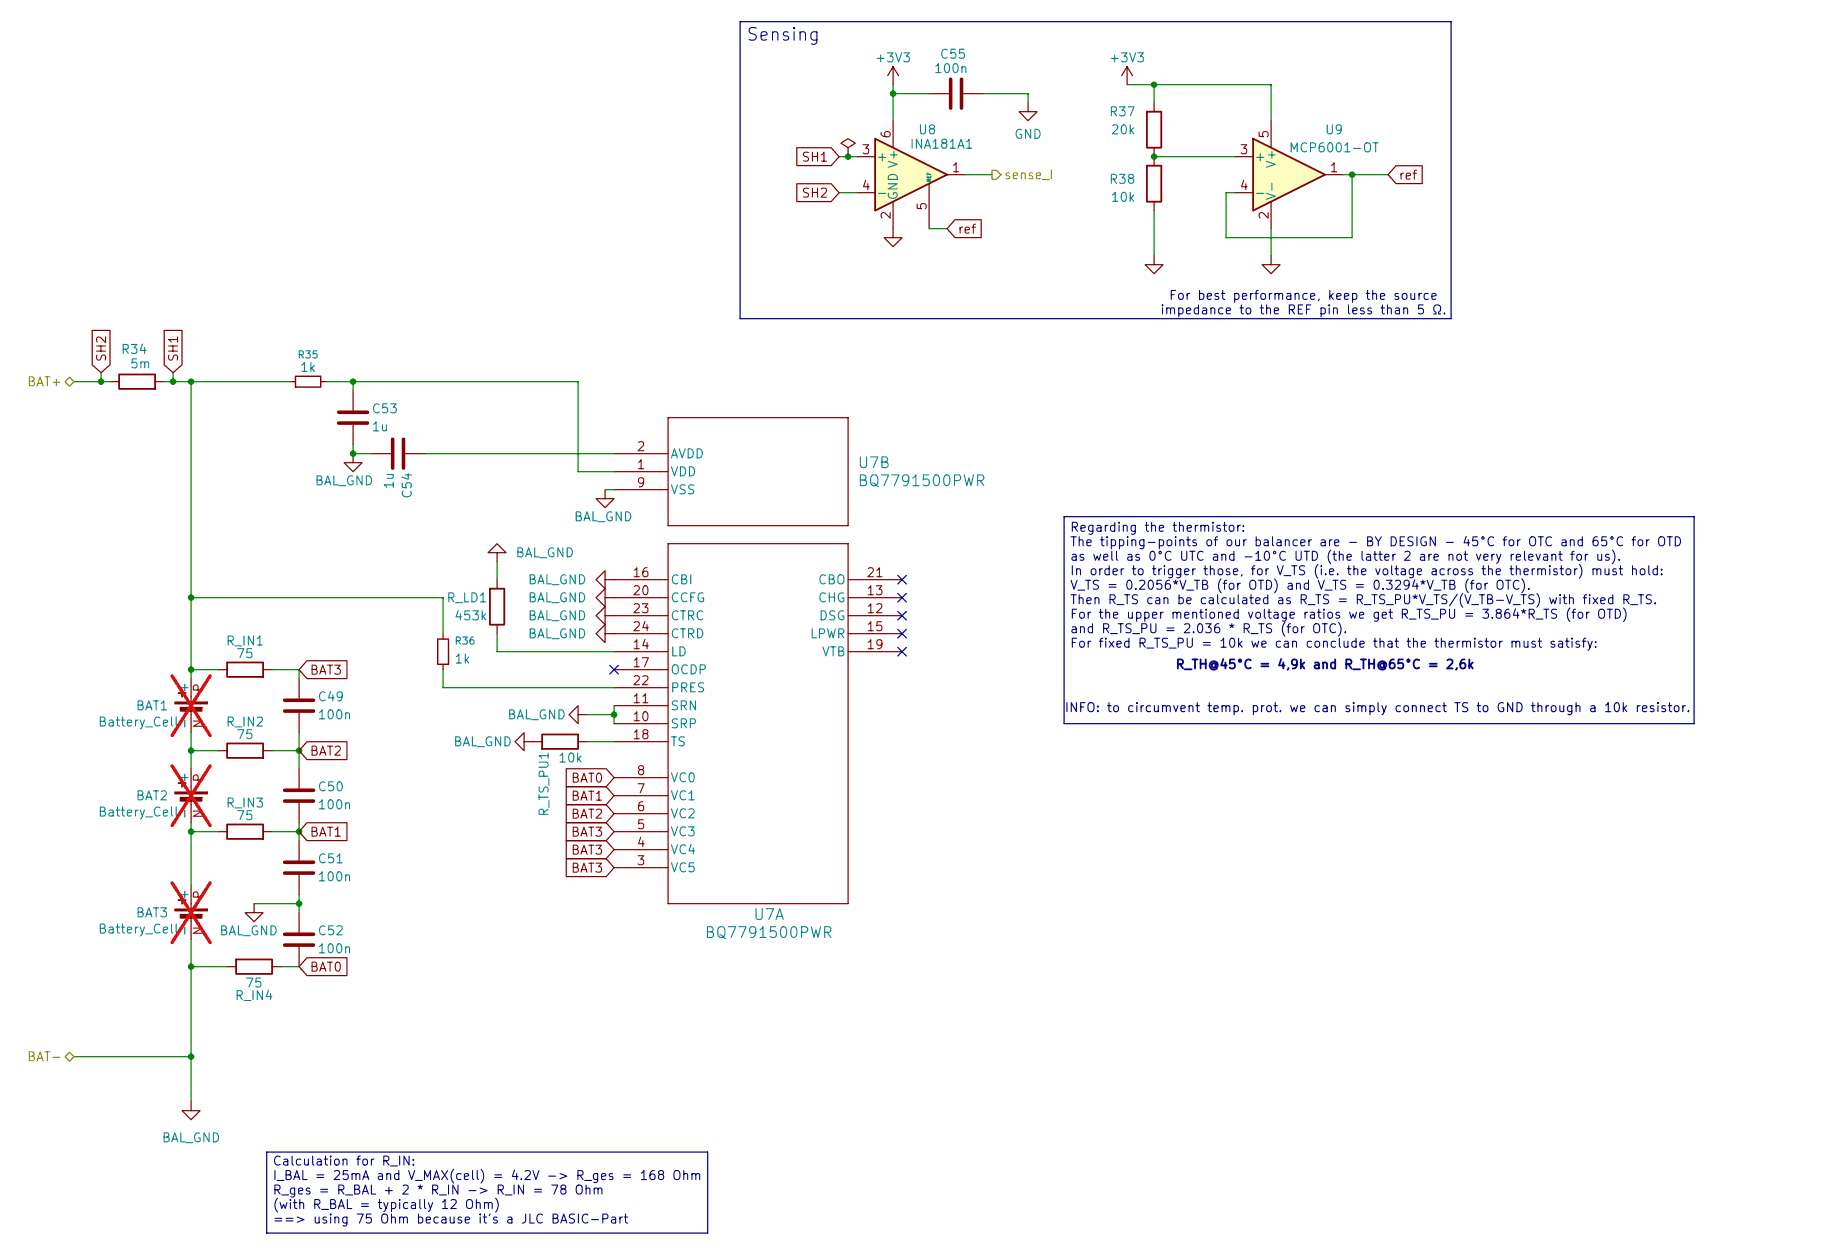
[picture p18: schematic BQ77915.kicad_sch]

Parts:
BAT1, BAT2, BAT3: Battery_Cell; BAT_1043; LCSC x; not fitted
C49, C50, C51, C52: 100n; C_0402_1005Metric; LCSC C307331
C53, C54: 1u; C_0402_1005Metric; LCSC C52923
C55: 100n; C_0402_1005Metric; LCSC C1525
R34: 5m; R_2512_6332Metric_Pad1.40x3.35mm_HandSolder; Part# DSLR-K-3-5F; LCSC C41382686
R35, R36: 1k; R_0402_1005Metric; LCSC C11702
R37: 20k; R_0402_1005Metric_Pad0.72x0.64mm_HandSolder; LCSC C25765
R38: 10k; R_0402_1005Metric_Pad0.72x0.64mm_HandSolder; LCSC C25744
R_IN1, R_IN2, R_IN3, R_IN4: 75; R_0603_1608Metric; LCSC C4275
R_LD1: 453k; R_0402_1005Metric; LCSC C27009
R_TS_PU1: 10k; R_0402_1005Metric; LCSC C25744
U7: BQ7791500PWR; TSSOP-24_4.4x7.8mm_P0.65mm; LCSC C2876946
U8: INA181A1; SOT-23-6; LCSC C2058943
U9: MCP6001-OT; SOT-23-5; LCSC C116490

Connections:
+3V3: C55.1, R37.2, U8.6 (V+), U9.5 (V+); also elsewhere on the board
/Balancer/sense_I: U8.1; also elsewhere on the board
BAL_GND: BAT3.N (-), C51.2, C52.1, C53.2, C54.2, C55.2, R38.1, R_IN4.2, R_LD1.2, R_TS_PU1.2, U7.9 (VSS), U7.10 (SRP), U7.11 (SRN), U7.16 (CBI), U7.20 (CCFG), U7.23 (CTRC), U7.24 (CTRD), U8.2 (GND), U9.2 (V-); also elsewhere on the board
BAT0: C52.2, R_IN4.1, U7.8 (VC0)
BAT1: C50.2, C51.1, R_IN3.2, U7.7 (VC1)
BAT2: C49.2, C50.1, R_IN2.2, U7.6 (VC2)
BAT3: C49.1, R_IN1.2, U7.3 (VC5), U7.4 (VC4), U7.5 (VC3)
unnamed: BAT1.N (-), BAT2.P (+), R_IN2.1
unnamed: BAT2.N (-), BAT3.P (+), R_IN3.1
unnamed: R_LD1.1, U7.14 (LD)
unnamed: R36.1, U7.22 (PRES)
unnamed: R_TS_PU1.1, U7.18 (TS)
unnamed: C54.1, U7.2 (AVDD)
unnamed: C53.1, R35.2, U7.1 (VDD)
unnamed: R37.1, R38.2, U9.3 (+)
SH1: BAT1.P (+), R34.2, R35.1, R36.2, R_IN1.1, U8.3 (+)
V_BAT: R34.1, U8.4 (-); also elsewhere on the board
ref: U8.5 (REF), U9.1, U9.4 (-)

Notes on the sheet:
For best performance, keep the source impedance to the REF pin less than 5 Ω.
R_TH@45°C = 4,9k and R_TH@65°C = 2,6k
INFO: to circumvent temp. prot. we can simply connect TS to GND through a 10k resistor.
Calculation for R_IN: I_BAL = 25mA and V_MAX(cell) = 4.2V -> R_ges = 168 Ohm R_ges = R_BAL + 2 * R_IN -> R_IN = 78 Ohm (with R_BAL = typically 12 Ohm) ==> using 75 Ohm because it's a JLC BASIC-Part
Regarding the thermistor: The tipping-points of our balancer are - BY DESIGN - 45°C for OTC and 65°C for OTD as well as 0°C UTC and -10°C UTD (the latter 2 are not very relevant for us). In order to trigger those, for V_TS (i.e. the voltage across the thermistor) must hold: V_TS = 0.2056*V_TB (for 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
Sensing

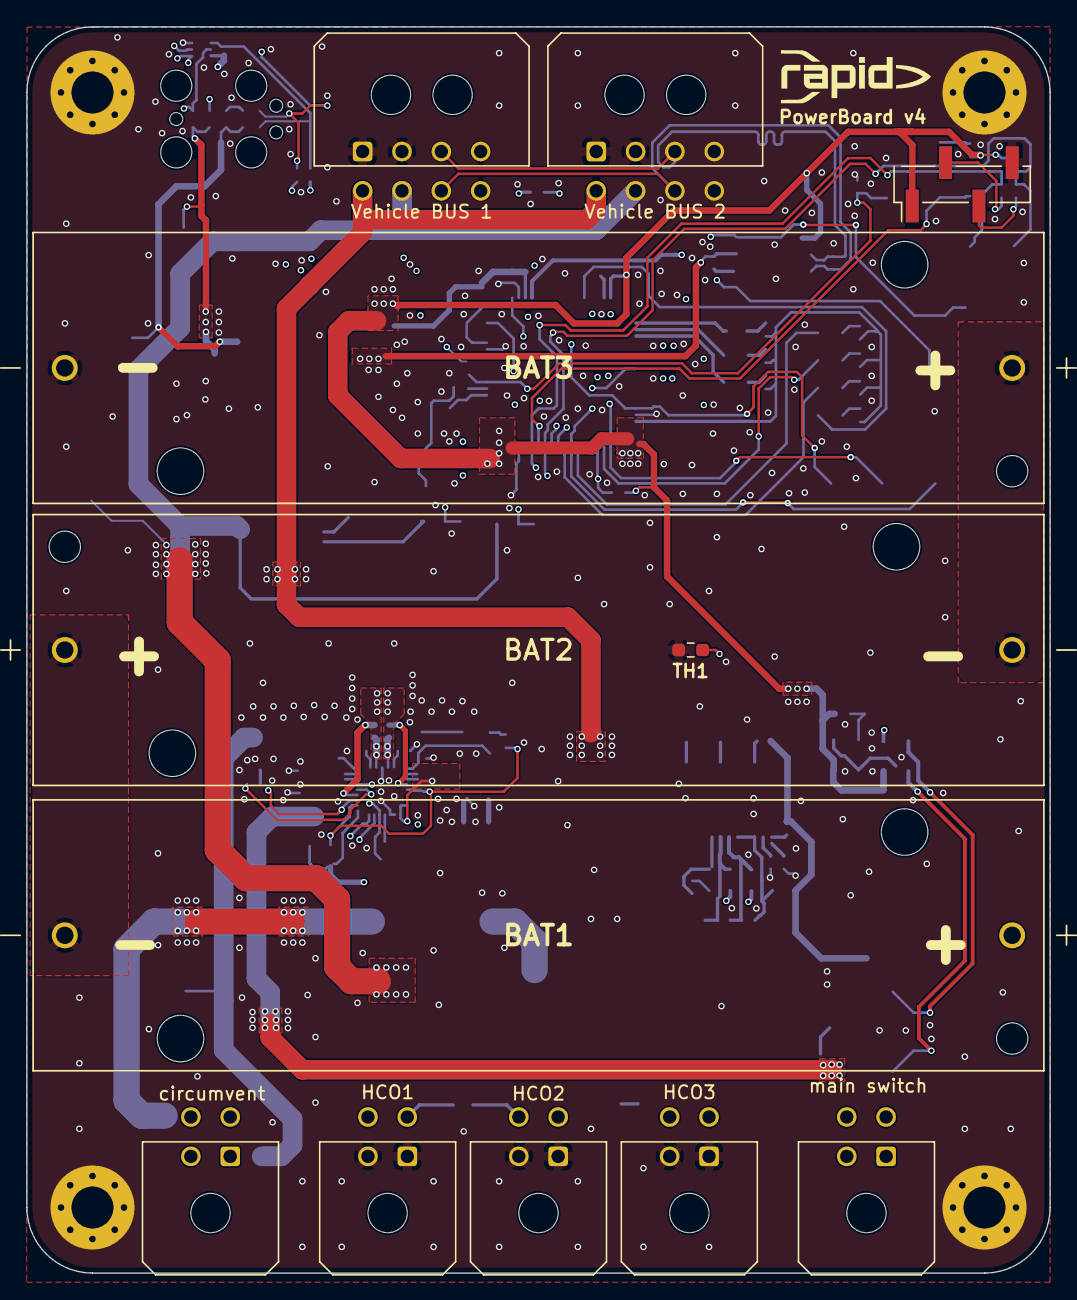
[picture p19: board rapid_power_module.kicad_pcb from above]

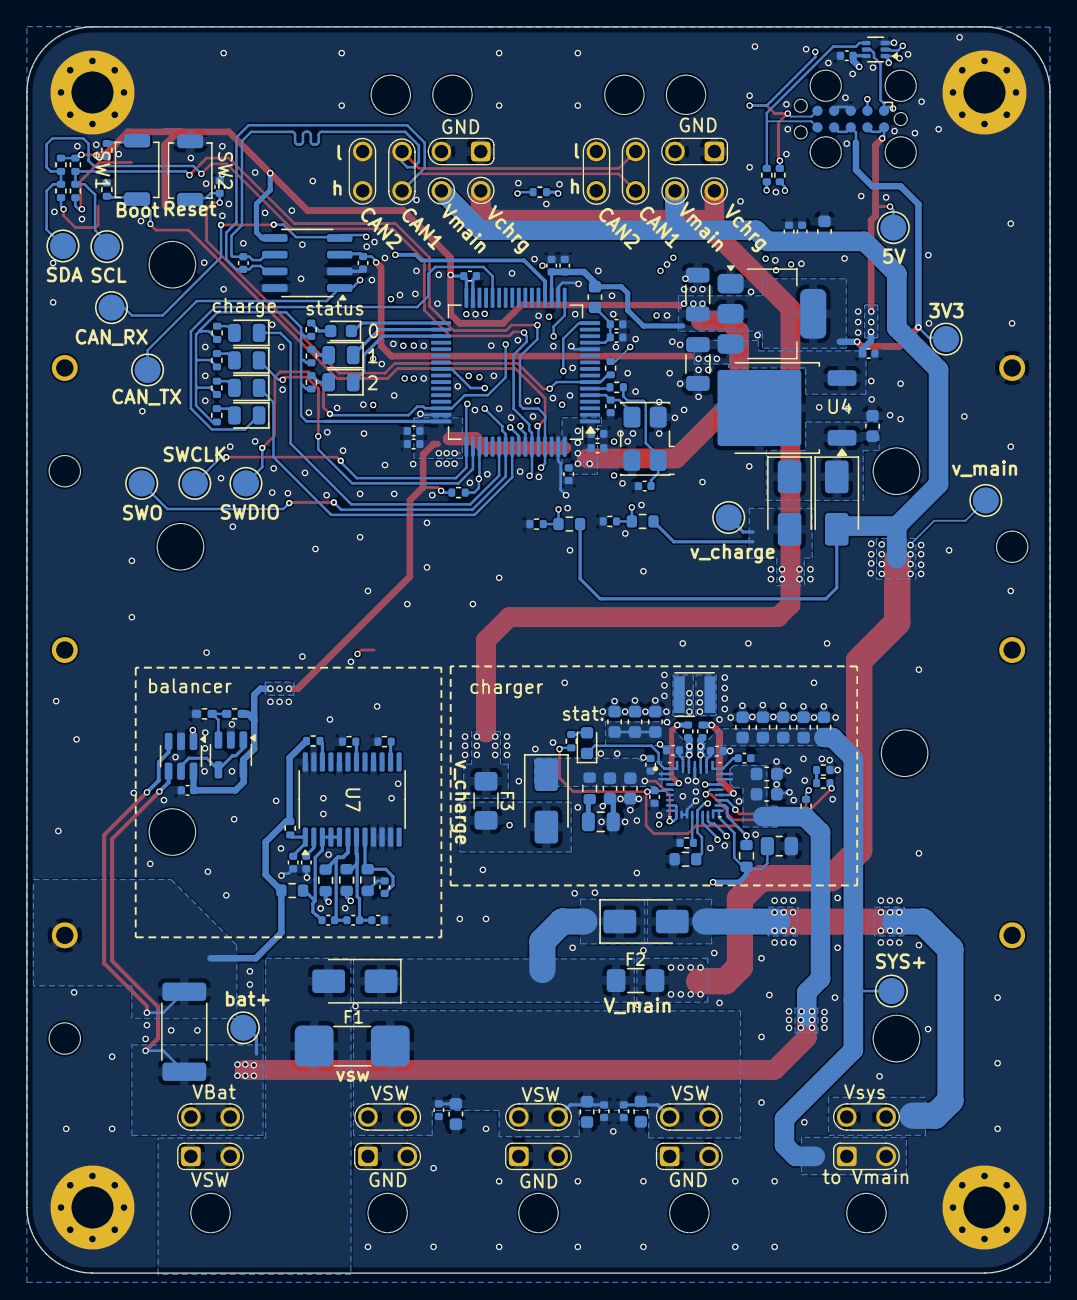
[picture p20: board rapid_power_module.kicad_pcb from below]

Board: 4 copper layers, 78.0 x 95.0 mm, 159 parts (143 on the bottom side), 86 nets.

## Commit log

2025-03-22 Added 2 ICs to library, added these ICs to the schaltplan. Added Readme Notes
    [0.PcbLib, 0.SchLib, bq25820-SchLib.sch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]
2025-04-23 Weitere Änderungen, aber noch nicht fertig
    [BQ25756_DESIGN-CALC-V01X3.xlsx, frodo_power_module.kicad_sch]
2025-04-29 Cell Balancer Reading Circuit cleaned up
    [V2.kicad_sch]
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2025-05-05 Added MCU and connected relevant Pins
    [V2.kicad_sch]
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2025-05-11 project cleanup and renaming
    [0.PcbLib, 0.SchLib, 430450400.step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]
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2025-05-11 Added Falstadt simulator file, incomplete
    [rapid_power_module.kicad_pcb, rapid_power_module.kicad_sch]
2025-05-12 added some connectors, components and todos
    [rapid_power_module.kicad_sch]
2025-05-19 Added BG25756 and exchanged it against BG25750 Changed the circuitry accordingly ToDo: Change values of resistors and caps to match final voltage and capacity
    [rapid_power_module.kicad_sch]
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2025-05-20 finalized excel sheet -> picture & values in scematic not adjusted jet, added some footprints and parts
    [BQ25756_DESIGN-CALC-V01X3.xlsx, rapid_power_module.kicad_sch]
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2025-05-23 changed values in the Buck Boost Section according to the excel sheet
    [rapid_power_module.kicad_sch]
2025-05-26 Added first design for the usb PD funtionality and added comments
    [rapid_power_module.kicad_sch]
2025-06-07 Added TODOs in Schematic
    [rapid_power_module.kicad_sch]
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2025-06-13 added charge indicator LEDs
    [rapid_power_module.kicad_sch]
2025-06-13 fixed vbus sense for usb pd
    [rapid_power_module.kicad_sch]
2025-06-13 balancer circuit with new chip
    [rapid_power_module.kicad_sch]
2025-06-13 changed GND in the PACK
    [rapid_power_module.kicad_sch]
2025-06-15 comments and a bit of cleanup
    [rapid_power_module.kicad_sch]
2025-06-23 changed back to bq76952
    [rapid_power_module.kicad_sch]
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2025-06-23 changed GND to VSS
    [rapid_power_module.kicad_sch]
2025-06-23 changed buck boost values according to the excel tool
    [rapid_power_module.kicad_sch]
2025-06-23 work on the Balancer
    [rapid_power_module.kicad_sch]
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2025-07-04 some comments and checking
    [rapid_power_module.kicad_sch]
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2025-07-07 Removed BJT as it is not required when not using REG1 and REG2
    [rapid_power_module.kicad_sch]
2025-07-21 Added Testpoints and some LCSC numbers
    [rapid_power_module.kicad_pcb, rapid_power_module.kicad_sch]
2025-07-28 Routing for 4 pin connectors
    [AONS66614.STEP, AONS66614.step, rapid_power_module.kicad_pcb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]
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2025-08-02 Added Footprints for MOSFETs
    [rapid_power_module.kicad_pcb, rapid_power_module.kicad_sch]
2025-08-02 Further Routing work and fixed the Q Pins
    [rapid_power_module.kicad_pcb, rapid_power_module.kicad_sch]
2025-08-03 Placed the NMOS near Inductor, moved STM out of the way and fixed the Battery Pins
    [rapid_power_module.kicad_pcb]
2025-08-03 Fixed wuerth cap footprints and values
    [rapid_power_module.kicad_pcb, rapid_power_module.kicad_sch]
2025-08-03 Added footprints and LCSC
    [rapid_power_module.kicad_pcb, rapid_power_module.kicad_sch]
2025-08-04 Added Diode and new connector type
    [rapid_power_module.kicad_sch]
2025-08-04 fix diode and more routing work
    [rapid_power_module.kicad_pcb, rapid_power_module.kicad_sch]
2025-08-04 Added Pin connections from USB PD to STM, removed non essential resistors
    [rapid_power_module.kicad_sch]
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2025-08-06 Fixed Balancer Pins so that LDO is not used and LDO input is grounded
    [rapid_power_module.kicad_sch]
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2025-08-07 check DRC and fix issues
    [rapid_power_module.kicad_pcb, usb_c.step]
2025-08-11 gnd changes in scematic and routing, tbc
    [rapid_power_module.kicad_pcb, rapid_power_module.kicad_sch]
2025-08-11 some changes in the scematic
    [rapid_power_module.kicad_sch]
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2025-08-12 croschecking scematic, some changes there and new routing approach
    [rapid_power_module.kicad_pcb, rapid_power_module.kicad_sch]
2025-08-14 scematic adaptations and routing
    [rapid_power_module.kicad_pcb, rapid_power_module.kicad_sch]
2025-08-15 Stop tracking embedded repo rapid_power_fw, added LD schemtaic
    [pin assignment.xlsx, rapid_power_module.kicad_sch]
2025-08-16 Added new Resistor for LD so that it can detect load and charger
    [rapid_power_module.kicad_sch]
2025-08-17 Continue with routing, esp. signal traces for mcu
    [rapid_power_module.kicad_pcb]
2025-08-17 Length matching, some cleanup, additional via placement
    [rapid_power_module.kicad_pcb]
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2025-08-17 Finishing touches (Zone optimizations to reduce antenna effect, wider battery connection zones)
    [rapid_power_module.kicad_pcb]
2025-08-17 Replace wrong battery manager footprint
    [rapid_power_module.kicad_pcb, rapid_power_module.kicad_sch]
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2025-09-02 Add async driver for BQ76952 battery monitor
    - Implemented the Bq76952 struct with methods for initialization, reading measurements, and configuring settings.
    - Added support for direct commands and subcommands as per the Technical Reference Manual (TRM).
    - Created register addresses and bit masks in a separate `regs` module.
    - Defined necessary types, enums, and error handling in the `types` module.
    - Included methods for voltage, current, temperature readings, and protection settings.
    - Added functionality for I2C address configuration and data memory writing.
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2025-09-24 Refactor BQ25756 configuration and enhance driver functionality
    - Updated default features in Cargo.toml
    - Added known errors section in README.md
    - Introduced new helper functions and improved existing methods in device.rs for better handling of DPM limits
    - Enhanced logging for charge and input current limits
    - Adjusted logging period and maximum charge/input current in config.rs
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2025-09-27 BQ25756: Fixed bit shift handling in ICHG and Voltage DPM
2025-09-27 Fixed max battery voltage
2025-10-13 fix broken trace
    [rapid_power_module.kicad_pcb]
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2025-12-03 added balancer thermistor info; changed MCU pinout to support CAN bootloading
    [BQ77915.kicad_sch, control_logic.kicad_sch]
2025-12-07 Changed Balancer layout to support OVP, UVP and UVP-circumvention; added UVP-circumvention arming connector
    [BQ77915.kicad_sch, control_logic.kicad_sch, rapid_power_module.kicad_sch]
2025-12-14 added explanations for balancer schematic and some component values
    [BQ77915.kicad_sch, control_logic.kicad_sch]
2025-12-15 changed balancer layout according to new requirements (i.e. removed OVP/UVP, OTP/UTP, OCP/UCP); reduced arming connectors to only one
    [BQ77915.kicad_sch, rapid_power_module.kicad_sch]
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2025-12-22 finalized new balancer layout (removed R_SNS and implemented the resulting consequences); removed charger shipping mode
    [BQ77915.kicad_sch, charger.kicad_sch, control_logic.kicad_sch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]
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2026-01-28 implemented changes according to errors found in the schematic design review (wip)
    [BQ77915.kicad_sch, charger.kicad_sch, control_logic.kicad_sch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]
2026-02-02 added missing footprints and validated all lcsc numbers; started pcb-layouting
    [BQ25798RQMR.step, BQ77915.kicad_sch, charger.kicad_sch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]
2026-03-09 started routing Please enter the commit message for your changes. Lines starting
    [charger.kicad_sch, control_logic.kicad_sch, rapid_power_module.kicad_pcb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]
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2026-04-21 implemented improvements based on feedback; Voltage/Current sensing still missing
    [BQ77915.kicad_sch, charger.kicad_sch, control_logic.kicad_sch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]
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2026-06-14 fix silkscreen issues and start implementing small layout improvements, cleanup repo
    [BQ77915.kicad_sch, charger.kicad_sch, control_logic.kicad_sch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]
2026-06-17 current state, shrinked board, some adaptions still neccesarry
    [0154005.stp, BQ77915.kicad_sch, Fuse_2410_0679L9200-05.stp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]
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
